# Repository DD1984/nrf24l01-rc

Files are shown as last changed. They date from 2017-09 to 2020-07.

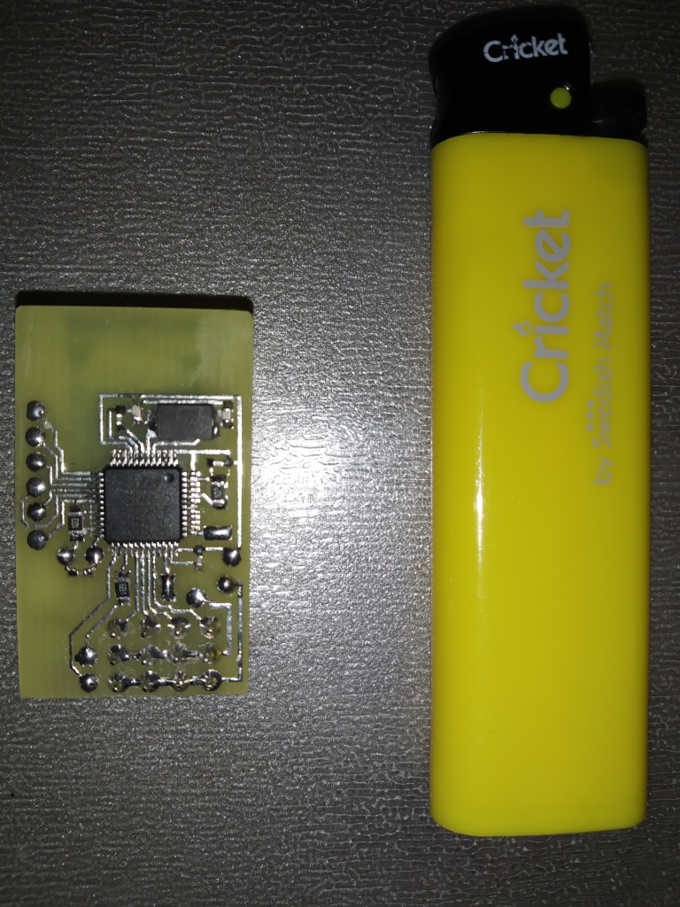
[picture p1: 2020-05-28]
stm32-nrf24l01-receiver/electronics/stm32f1/top.jpg

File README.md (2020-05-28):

# nRF24-based RC car receiver, compatible with HobbyKing HK310 and Turnigy 3XS

This project includes **electronics** and **firmware** to build **surface RC receivers** that can replace the HobbyKing [HKR3000](http://hobbyking.com/hobbyking/store/__12187__HK_3000_3ch_2_4ghz_FHSS_RX_suit_the_HK310_Transmitter.html) and [XR3100](http://hobbyking.com/hobbyking/store/__22910__HK3100_3ch_2_4ghz_FHSS_Micro_RX_suits_HK310_Turnigy_3XS_TX_.html) receivers. They can be used with the [HK300](http://hobbyking.com/hobbyking/store/__12177__HK_300_3_Channel_2_4ghz_FHSS_Ground_Radio.html), [HK310](http://hobbyking.com/hobbyking/store/__12181__HK_310_3_Channel_2_4ghz_FHSS_Ground_Radio.html) and [Turnigy 3XS](http://hobbyking.com/hobbyking/store/__24905__Turnigy_3XS_FHSS_2_4GHz_3_Channel_Radio_System.html) RC car radio systems.

The receivers make use of off-the-shelf inexpensive RF modules.

Two variants are provided:

- [lpc812-nrf24l01](lpc812-nrf24l01-receiver/): NRF24L01+ module plus a [NXP LPC812](http://www.nxp.com/products/microcontrollers/cortex_m0_m0/series/LPC800.html) MCU
- [nrf24le1](nrf24le1-receiver/): Using a NRF24LE1 module (integrated 8051 MCU)

**Now the third variant is available:**

- [stm32-nrf24l01](stm32-nrf24l01-receiver/): NRF24L01+ module plus a cheap STM32F030F4P6 MCU

**Fourth variant is available:**
- [stm32-nrf24l01](stm32-nrf24l01-receiver/): NRF24L01+ module (smd mount) plus a STM32F100C4T6 MCU (work on stm32vldiscovery too)

Technical information about the inner working of the receivers can be found
in **[hkr3000-info.md](doc/hkr3000-info.md)**.

## Advantages of the NRF24L01+ - LPC812 version

- Easily obtainable and very low cost NRF module (less than USD 1 including shipping in qty 10 on eBay, Aliexpress)
- Very precise servo pulses due to LPC812 timer hardware
- ARM Cortex-M0 32-bit CPU is easy to program for with the GCC ARM compiler
- No proprietary programmer required as the MCU has a ROM bootloader that can be flashed with an  USB-to-serial dongle
- Servo pulses can be updated down to every 5 ms (200 Hz). In theory this may provide better response but in practice the transmitter would need to be modified to fully take
advantage of this fact.
- UART output using the LANE Boys RC [preprocessor protocol](http://laneboysrc.blogspot.com/2012/12/pre-processor-for-diy-rc-light.html), e.g. to hook up the [DIY RC light controller](https://github.com/laneboysrc/rc-light-controller) with a single servo cable.

Downsides:

- Requires a PCB and intermediate SMD soldering skills
- No CPPM output (but it has a UART output that can carry CPPM-like data and more)

## Advantages of the NRF24LE1 version

- Low part count: NRF24LE1 module, voltage regulator, a few capacitors; done!
- Simple to build even on a breadboard
- CPPM output
- UART output using the LANE Boys RC [preprocessor protocol](http://laneboysrc.blogspot.com/2012/12/pre-processor-for-diy-rc-light.html), e.g. to hook up the [DIY RC light controller](https://github.com/laneboysrc/rc-light-controller) with a single servo cable. Baudrate is limited to 38400 though.

Downsides:

- NRF24LE1 module is more expensive than NRF24L01 and harder to find
- Requires special programming hardware. Multiple open-source versions can be found on the Internet.
- Servo pulses are software timed, hence slightly jittery despite using interrupts. Note that the firmware included in this project is improved over the original HKR3000 and XR3100 firmware, which regularly extends servo pulses by 16 us due to poor interrupt logic implementation.
- For the PCB provided in this project you need to get the NRF24LE1 module version that has an SMD crystal (size 21 x 15 mm)

The NRF24LE1 firmware included in this project can be compiled to be compatible with the HKR3000 and XR3100 hardware. However, since those receivers use the OTP version (NRF24LE1G) one would have to replace the chip with the NR24LE1E versions to be able to use it.

## Advantages of the NRF24L01+ - STM32F0 version

- Cheap and easily accessible MCU
- Free version of Keil MDK for STM32F0
- precise PWM due to hardware timer
- PWM frequency up to 200 Hz independ for CH1 and CH2/CH3
- One sided PCB with two jumper wire only

Downsides:

- 3 channel PWM output only

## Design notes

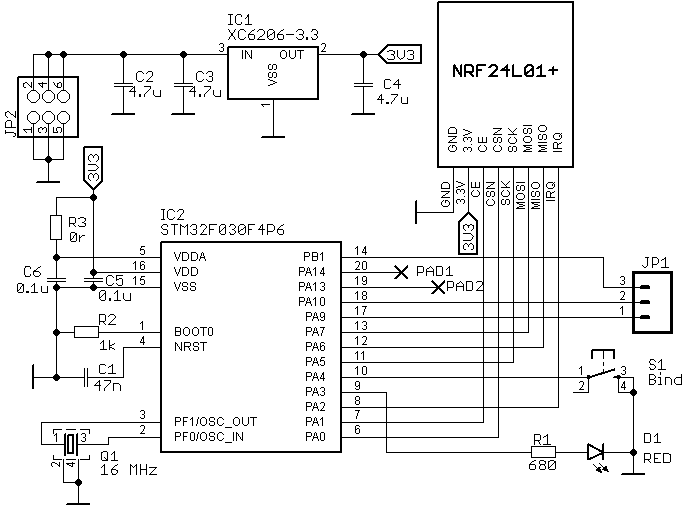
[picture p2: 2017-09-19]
stm32-nrf24l01-receiver/electronics/stm32f0/schematic.png

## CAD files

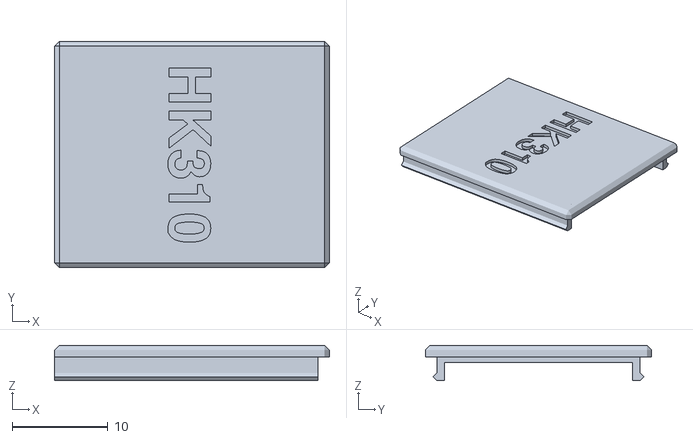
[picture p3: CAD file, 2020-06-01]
stm32-nrf24l01-receiver/electronics/stm32f1/box/box_top.stl
28.7 x 23.6 x 3.70

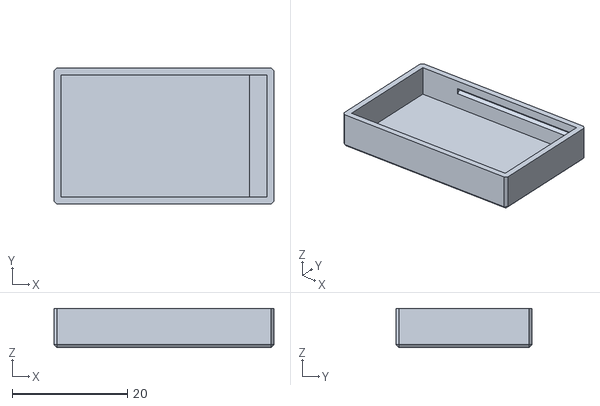
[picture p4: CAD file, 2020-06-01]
stm32-nrf24l01-receiver/electronics/stm32f1/box/box_bottom.stl
38.1 x 23.6 x 6.80

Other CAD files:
stm32-nrf24l01-receiver/electronics/stm32f1/box/rx_box.f3d

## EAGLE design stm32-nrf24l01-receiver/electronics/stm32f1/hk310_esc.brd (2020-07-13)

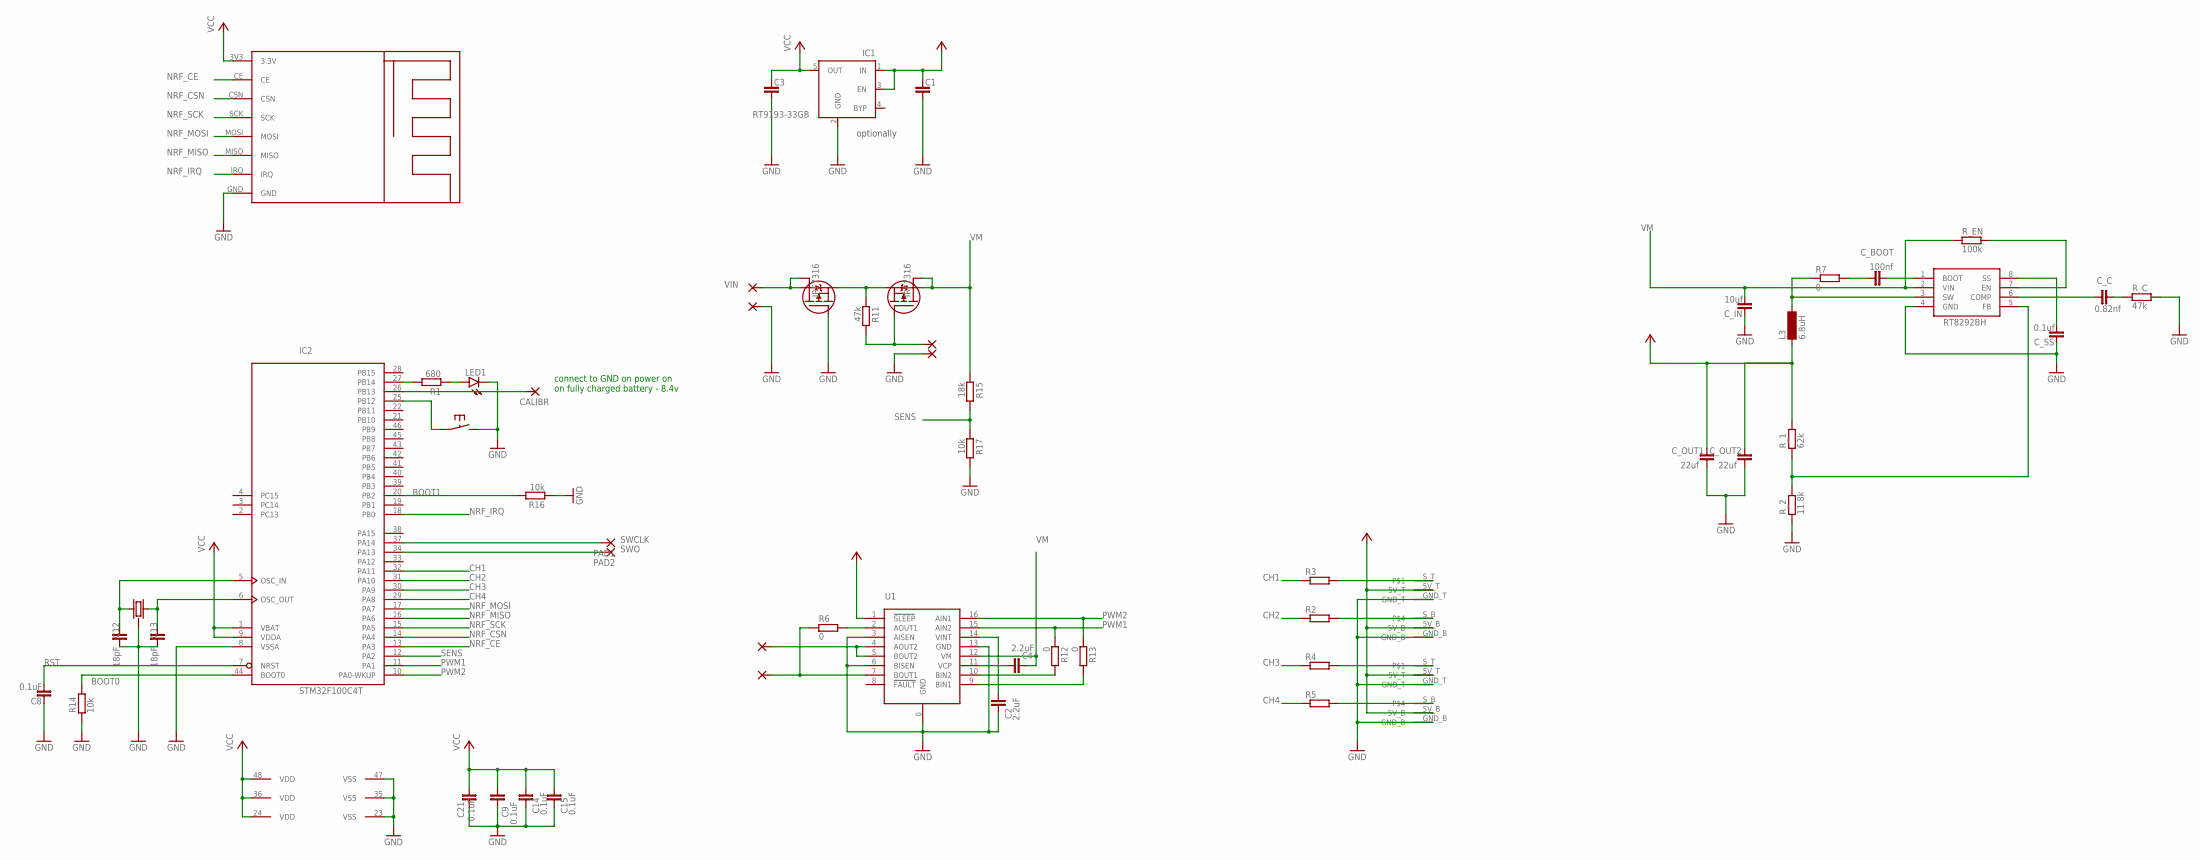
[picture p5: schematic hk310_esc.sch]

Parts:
C1, C3: C_0805; C0805
C2, C4: 2.2uF; C0805
C8, C9, C14, C15, C21: 0.1uF; C0603
C12, C13: 18pF; C0603
CALIBR: SMD2; SMD1,27-2,54
C_BOOT: 100nf; C0402
C_C: 0.82nf; C0402
C_IN: 10uf; C1206
C_OUT1, C_OUT2: 22uf; C0805
C_SS: 0.1uf; C0402
IC1: RT9193-33GB; SOT23-5
IC2: STM32F100C4T; LQFP48
L3: 6.8uH; MS85
LED1: LED; SMARTLED-TTW
PAD1, PAD2: SMD2; SMD1,27-2,54
PAD3, PAD4, PAD5, PAD6, PAD7, PAD8: WIREPADSMD5-1,8; 5-1,8
R1: 680; R0805
R2, R3, R4, R5: R-EU_R1206; R1206
R6, R7, R12, R13: 0; R1206
R11: 47k; R0805
R14, R16, R17: 10k; R0805
R15: 18k; R0805
RT8292BH: RT8292B; SO8-2
R_1: 62k; R0402
R_2: 11.8k; R0402
R_C: 47k; R0402
R_EN: 100k; R0402
U1: DRV8833; PWP16
U$1: NRF24MINI
U$2, U$3: PINHEAD_SMD
U$5: IRF7104; SO8-2
U$6: 8Mhz; CRYSTAL_3PINS
U$7: SMALL_BUTTON

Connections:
+5V: C1.1, C_OUT1.2, C_OUT2.2, IC1.1 (IN), IC1.3 (EN), L3.1, R_1.2, U1.1 (!SLEEP), U$2.5V_B, U$2.5V_T, U$3.5V_B, U$3.5V_T
BOOT0: IC2.44 (BOOT0), R14.2
BOOT1: IC2.20 (PB2), R16.2
CH1: IC2.32 (PA11), R3.1
CH2: IC2.31 (PA10), R2.1
CH3: IC2.30 (PA9), R4.1
CH4: IC2.29 (PA8), R5.1
GND: C1.2, C2.1, C3.2, C8.1, C9.1, C12.1, C13.1, C14.1, C15.1, C21.1, C_IN.1, C_OUT1.1, C_OUT2.1, C_SS.1, IC1.2 (GND), IC2.8 (VSSA), IC2.23 (VSS), IC2.35 (VSS), IC2.47 (VSS), LED1.C@1 (C), PAD5.1, PAD8.1, R14.1, R16.1, R17.2, RT8292BH.4 (GND), R_2.1, R_C.2, U1.0 (GND), U1.3 (AISEN), U1.6 (BISEN), U1.13 (GND), U$1.GND, U$2.GND_B, U$2.GND_T, U$3.GND_B, U$3.GND_T, U$5.4 (G), U$6.GND, U$7.2_1 (2), U$7.2_2 (2)
unnamed: IC2.25 (PB12), U$7.1_1 (1), U$7.1_2 (1)
unnamed: IC2.27 (PB14), R1.2
unnamed: LED1.A@1 (A), R1.1
unnamed: PAD3.1, U1.4 (AOUT2), U1.5 (BOUT2)
unnamed: R6.2, U1.2 (AOUT1)
unnamed: C2.2, U1.14 (VINT)
unnamed: C4.2, U1.11 (VCP)
unnamed: CALIBR.1, IC2.26 (PB13)
unnamed: C12.2, IC2.5 (OSC_IN), U$6.P$1
unnamed: R12.2, U1.10 (BIN2)
unnamed: R3.2, U$2.S_T
unnamed: R2.2, U$2.S_B
unnamed: R4.2, U$3.S_T
unnamed: R5.2, U$3.S_B
unnamed: PAD7.1, R6.1, U1.7 (BOUT1)
unnamed: C_BOOT.1, R7.2
unnamed: C13.2, IC2.6 (OSC_OUT), U$6.P$2
unnamed: PAD6.1, R11.2, U$5.2 (G)
unnamed: R13.2, U1.9 (BIN1)
unnamed: RT8292BH.7 (EN), R_EN.2
unnamed: C_SS.2, RT8292BH.8 (SS)
unnamed: C_BOOT.2, RT8292BH.1 (BOOT)
unnamed: L3.2, R7.1, RT8292BH.3 (SW)
unnamed: RT8292BH.5 (FB), R_1.1, R_2.2
unnamed: C_C.2, R_C.1
unnamed: C_C.1, RT8292BH.6 (COMP)
NRF_CE: IC2.13 (PA3), U$1.CE
NRF_CSN: IC2.14 (PA4), U$1.CSN
NRF_IRQ: IC2.18 (PB0), U$1.IRQ
NRF_MISO: IC2.16 (PA6), U$1.MISO
NRF_MOSI: IC2.17 (PA7), U$1.MOSI
NRF_SCK: IC2.15 (PA5), U$1.SCK
PWM1: IC2.11 (PA1), R12.1, U1.15 (AIN2)
PWM2: IC2.10 (PA0-WKUP), R13.1, U1.16 (AIN1)
RST: C8.2, IC2.7 (NRST)
SENS: IC2.12 (PA2), R15.2, R17.1
SWCLK: IC2.37 (PA14), PAD1.1
SWO: IC2.34 (PA13), PAD2.1
VCC: C3.1, C9.2, C14.2, C15.2, C21.2, IC1.5 (OUT), IC2.1 (VBAT), IC2.9 (VDDA), IC2.24 (VDD), IC2.36 (VDD), IC2.48 (VDD), U$1.3V3 (3.3V)
VIN: PAD4.1, U$5.5 (D), U$5.6 (D)
VIN_PROT: R11.1, U$5.1 (S), U$5.3 (S)
VM: C4.1, C_IN.2, R15.1, RT8292BH.2 (VIN), R_EN.1, U1.12 (VM), U$5.7 (D), U$5.8 (D)

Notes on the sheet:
optionally
connect to GND on power on on fully charged battery - 8.4v

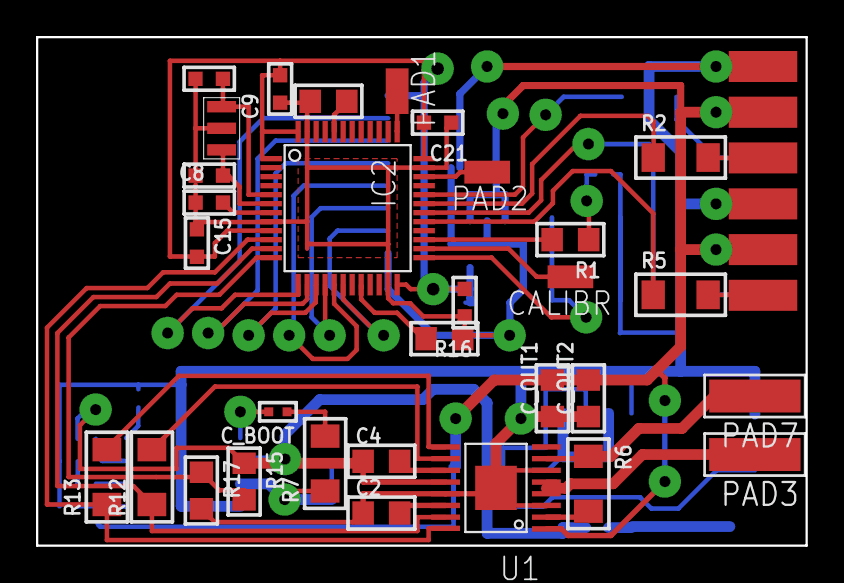
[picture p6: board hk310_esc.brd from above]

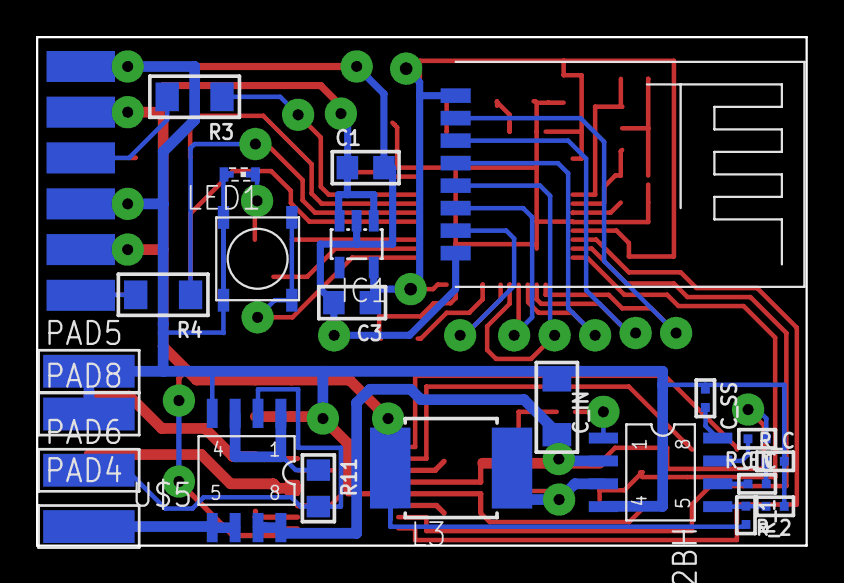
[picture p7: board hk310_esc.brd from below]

Board: 2 copper layers, 42.8 x 28.2 mm, 56 parts (25 on the bottom side), 50 nets.

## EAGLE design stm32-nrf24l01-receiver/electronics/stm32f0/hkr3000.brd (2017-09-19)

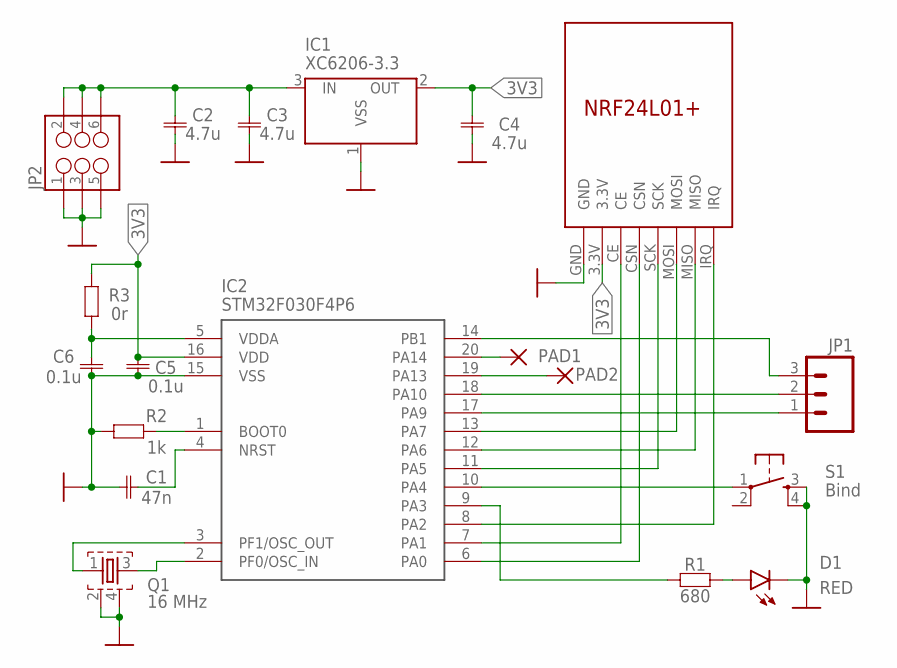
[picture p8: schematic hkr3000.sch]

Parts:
C1: 47n; 0402
C2, C3, C4: 4.7u; 0805
C5, C6: 0.1u; 0402
D1: RED; LED-0603
IC1: XC6206-3.3; XC6206_SOT-23
IC2: STM32F030F4P6; TSSOP-20
JP1: M03PTH; 1X03
JP2: M03X2POGO_PINS; 2X3_POGO
PAD1, PAD2: SMD2; SMD1,27-2,54
Q1: 16 MHz; FA-20H
R1: 680; 0402
R2: 1k; 0402
R3: 0r; 0603
S1: Bind; TACTILE-PTH
U$1: NRF24L01

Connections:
3V3: C4.P$2, C5.P$2, IC1.2 (OUT), IC2.16 (VDD), R3.P$2, U$1.3.3V
3V3-1: C6.P$2, IC2.5 (VDDA), R3.P$1
GND: C1.P$1, C2.P$1, C3.P$1, C4.P$1, C5.P$1, C6.P$1, D1.C, IC1.1 (VSS), IC2.15 (VSS), JP2.P$1 (1), JP2.P$3 (3), JP2.P$5 (5), Q1.2, Q1.4, R2.P$1, S1.3, S1.4, U$1.GND
unnamed: C2.P$2, C3.P$2, IC1.3 (IN), JP2.P$2 (2), JP2.P$4 (4), JP2.P$6 (6)
unnamed: D1.A, R1.P$2
unnamed: IC2.20 (PA14), PAD1.1
unnamed: IC2.11 (PA5), U$1.SCK
unnamed: IC2.12 (PA6), U$1.MISO
unnamed: IC2.13 (PA7), U$1.MOSI
unnamed: IC2.17 (PA9), JP1.1
unnamed: IC2.18 (PA10), JP1.2
unnamed: IC2.14 (PB1), JP1.3
unnamed: IC2.2 (PF0/OSC_IN), Q1.3
unnamed: IC2.3 (PF1/OSC_OUT), Q1.1
unnamed: C1.P$2, IC2.4 (NRST)
unnamed: IC2.1 (BOOT0), R2.P$2
unnamed: IC2.9 (PA3), R1.P$1
unnamed: IC2.19 (PA13), PAD2.1
unnamed: IC2.7 (PA1), U$1.CE
unnamed: IC2.6 (PA0), U$1.CSN
unnamed: IC2.8 (PA2), U$1.IRQ
unnamed: IC2.10 (PA4), S1.1

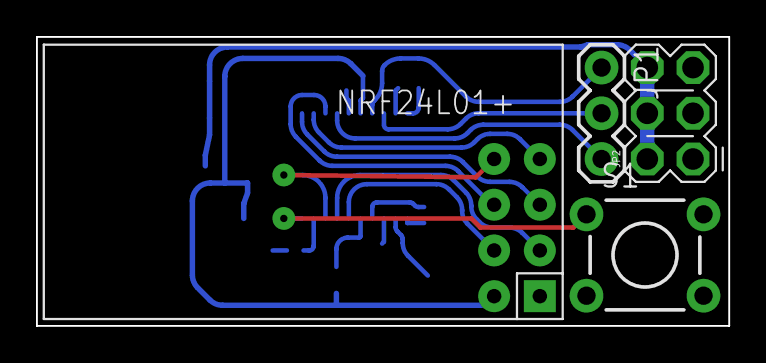
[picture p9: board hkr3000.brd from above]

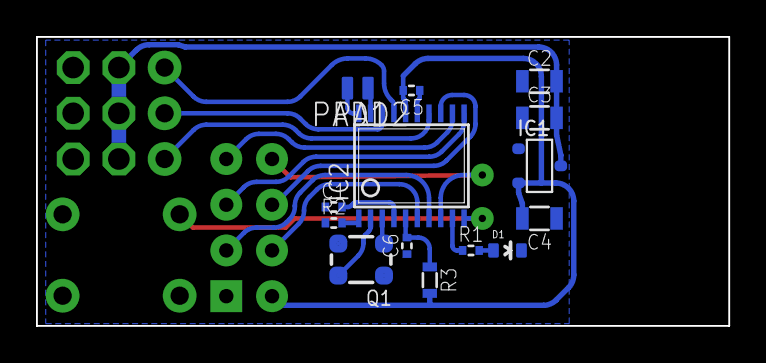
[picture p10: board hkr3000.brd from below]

Board: 2 copper layers, 38.5 x 16.1 mm, 19 parts (15 on the bottom side), 22 nets.

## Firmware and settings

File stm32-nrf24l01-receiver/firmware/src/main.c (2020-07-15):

/******************************************************************************

    Application entry point.

    Contains the main loop and the hardware initialization.

******************************************************************************/
#include <stdio.h>
#include <stdbool.h>

#include "platform.h"

#include "spi.h"
#include "rc_receiver.h"

#ifdef ESC
#include "esc.h"
#include "tune.h"
#include "adc.h"
#endif


#define IWDG_REFRESH        0x0000AAAA
#define IWDG_START          0x0000CCCC
#define IWDG_WRITE_ACCESS   0x00005555


// Global flag that is true for one mainloop every __SYSTICK_IN_MS
bool systick;
static volatile uint32_t systick_count;

// ****************************************************************************
static void service_systick(void)
{
    if (!systick_count) {
        systick = false;
        return;
    }

    systick = true;

    // Disable the SysTick interrupt. Use memory barriers to ensure that no
    // interrupt is pending in the pipeline.
    // More info:
    // http://infocenter.arm.com/help/index.jsp?topic=/com.arm.doc.dai0321a/BIHHFHJD.html
    SysTick->CTRL &= ~(1 << 1);
    __DSB();
    __ISB();
    --systick_count;
    SysTick->CTRL |= (1 << 1);      // Re-enable the system tick interrupt
}

// ****************************************************************************
#ifdef STM32F1
void EXTI0_IRQHandler (void)
#else
void EXTI2_3_IRQHandler (void)
#endif
{
    uint32_t status = EXTI->PR;
    uint32_t pending = 0;

#ifdef STM32F1
    if (status & EXTI_PR_PR0)
    {
        pending |= EXTI_PR_PR0;
        rf_interrupt_handler();
    }
#else
    if (status & EXTI_PR_PR2)
    {
        pending |= EXTI_PR_PR2;
        rf_interrupt_handler();
        //GPIO_LED_ON();
    }
#endif

    EXTI->PR = pending;
}

// ****************************************************************************
void TIM3_IRQHandler (void)
{
    uint16_t status = TIM3->SR;
    
    if (status & TIM_SR_UIF)
    {
        hop_timer_handler();
        status &= ~(TIM_SR_UIF);
    }

    TIM3->SR = status;
}

// ****************************************************************************
void SysTick_Handler (void)
{
    if (SysTick->CTRL & (1 << 16)) {       // Read and clear Countflag
        ++systick_count;
    }
}


// ****************************************************************************
static void init_hardware(void)
{
#ifdef STM32F1
    /**
     * PB14    - LED
     * PB13    - BAT CALIBR
     * PB12    - BIND
     *
     * PA4     - NRF_CSN
     * PA3     - NRF_CE
     * PB0     - NRF_IRQ
     * PA5     - NRF_SCK
     * PA6     - NRF_MISO
     * PA7     - NRF_MOSI
     *
     * PA11    - CH1 - TIM1_CH4
     * PA10    - CH2 - TIM1_CH3
     * PA9     - CH3 - TIM1_CH2
     * PA8     - CH4 - TIM1_CH1 - for future use
     */
    /* GPIO config */
    RCC->APB2ENR |= RCC_APB2ENR_IOPAEN | RCC_APB2ENR_IOPBEN | RCC_APB2ENR_IOPCEN | RCC_APB2ENR_AFIOEN;
    //PB14 - LED
    GPIOB->CRH &= ~(GPIO_CRH_CNF14 | GPIO_CRH_MODE14);
    GPIOB->CRH |= GPIO_CRH_MODE14_1; //2mhz out push-pull
    //PB12 - BIND
    GPIOB->CRH &= ~(GPIO_CRH_CNF12 | GPIO_CRH_MODE12);
    GPIOB->CRH |= GPIO_CRH_CNF12_1; //input push-pull
    GPIOB->BSRR = GPIO_BSRR_BS12; //pull up
#ifdef ESC
    //PB13 - BAT CALIBR
    GPIOB->CRH &= ~(GPIO_CRH_CNF13 | GPIO_CRH_MODE13);
    GPIOB->CRH |= GPIO_CRH_CNF13_1; //input push-pull
    GPIOB->BSRR = GPIO_BSRR_BS13; //pull up
#endif

    //PA4 - NRF_CSN, PA3 - NRF_CE
    GPIOA->CRL &= ~(GPIO_CRL_CNF4 | GPIO_CRL_MODE4 | GPIO_CRL_CNF3 | GPIO_CRL_MODE3);
    GPIOA->CRL |= GPIO_CRL_MODE4_0 | GPIO_CRL_MODE3_0; //10mhz out push-pull
    //PB0 - NRF_IRQ
    GPIOB->CRL &= ~(GPIO_CRL_CNF0 | GPIO_CRL_MODE0);
    GPIOB->CRL |= GPIO_CRL_CNF0_1; //input push-pull
    GPIOB->BSRR = GPIO_BSRR_BS0; //pull up

    //PA5, PA7
    GPIOA->CRL &= ~(GPIO_CRL_CNF5 | GPIO_CRL_MODE5 | GPIO_CRL_CNF7 | GPIO_CRL_MODE7);
    GPIOA->CRL |= GPIO_CRL_CNF5_1 | GPIO_CRL_MODE5_0 | GPIO_CRL_CNF7_1 | GPIO_CRL_MODE7_0; //10mhz alt push-pull
    //PA6 - floating input (do nothing)

    //PA11, PA10, PA9, PA8
    GPIOA->CRH &= ~(GPIO_CRH_CNF11 | GPIO_CRH_MODE11
                 | GPIO_CRH_CNF10 | GPIO_CRH_MODE10
                 | GPIO_CRH_CNF9 | GPIO_CRH_MODE9
                 | GPIO_CRH_CNF8 | GPIO_CRH_MODE8);
    GPIOA->CRH |= GPIO_CRH_CNF11_1 | GPIO_CRH_MODE11_0
               | GPIO_CRH_CNF10_1 | GPIO_CRH_MODE10_0
               | GPIO_CRH_CNF9_1 | GPIO_CRH_MODE9_0
               | GPIO_CRH_CNF8_1 | GPIO_CRH_MODE8_0; //10mhz alt push-pull


#else

    /**
     * PA0     - NRF_CSN
     * PA1     - NRF_CE
     * PA2     - NRF_IRQ
     * PA3     - LED
     * PA4     - BIND
     * PA5     - NRF_SCK
     * PA6     - NRF_MISO
     * PA7     - NRF_MOSI
     * PA9     - CH3 - TIM1_CH2
     * PA10    - CH2 - TIM1_CH3
     * PB1     - CH1 - TIM14_CH1
     */
    /* GPIO config */
    RCC->AHBENR |= RCC_AHBENR_GPIOAEN | RCC_AHBENR_GPIOBEN;

    GPIOA->MODER  &= ~(0x003CFFFF);
    GPIOA->MODER  |=   0x0028A845;
    GPIOA->OSPEEDR|=   0x003CCCCF;
    GPIOA->PUPDR  |=   0x00001110;
    GPIOA->AFR[0] &= ~(0xFFF00000);
    GPIOA->AFR[0] |=   0x00000000;
    GPIOA->AFR[1] &= ~(0x00000FF0);
    GPIOA->AFR[1] |=   0x00000220;
    

    GPIOB->MODER  &= ~(0x0000000C);
    GPIOB->MODER  |=   0x00000008;
    GPIOB->OSPEEDR|=   0x0000000C;
    GPIOB->AFR[0] &= ~(0x000000F0);
    GPIOB->AFR[0] |=   0x00000000;
    
#endif

    /* EXTI config */
#ifdef STM32F1
    AFIO->EXTICR[0] &= ~(AFIO_EXTICR1_EXTI0);
    AFIO->EXTICR[0] |=   AFIO_EXTICR1_EXTI0_PB;

    EXTI->FTSR |= EXTI_FTSR_TR0; /* Falling trigger event configuration */
    EXTI->IMR  |= EXTI_IMR_MR0;  /* Interrupt Mask on line 0 */
#else
    SYSCFG->EXTICR[0] &= ~(SYSCFG_EXTICR1_EXTI2);
    SYSCFG->EXTICR[0] |=   SYSCFG_EXTICR1_EXTI2_PA;
 
    EXTI->FTSR |= EXTI_FTSR_TR2; /* Falling trigger event configuration */
    EXTI->IMR  |= EXTI_IMR_MR2;  /* Interrupt Mask on line 2 */
#endif


    /* PWM Timers config */
#ifndef STM32F1
    RCC->APB1ENR |= RCC_APB1ENR_TIM14EN;
    TIM14->PSC = (24-1); /* Ftim = 2 Mhz */
    TIM14->ARR = ((2000000/CH1_FREQUENCY) - 1);
    TIM14->CCR1 = 2*1500; /* width = 1.5 ms */
    TIM14->CCMR1 |= TIM_CCMR1_OC1M_2 | TIM_CCMR1_OC1M_1 | TIM_CCMR1_OC1PE;
    TIM14->CCER |= TIM_CCER_CC1E;
    TIM14->CR1 |= TIM_CR1_CEN;
    TIM14->EGR = TIM_EGR_UG;	//	generate event and reload PSC
    while ((TIM14->SR & TIM_SR_UIF) == 0){}
    TIM14->SR = 0;
#endif
    
    RCC->APB2ENR |= RCC_APB2ENR_TIM1EN;   
#ifdef STM32F1
    TIM1->PSC = (SystemCoreClock / 1000000 / 2 - 1); /* Ftim = 2 Mhz */
    TIM1->ARR = ((2000000/CH2_CH3_FREQUENCY) - 1);
    TIM1->CCR1 = TIM1->CCR2 = TIM1->CCR3= TIM1->CCR4 = 2*1500; /* width = 1.5 ms */

    TIM1->CCMR1 = TIM_CCMR1_OC1M_2 | TIM_CCMR1_OC1M_1 | TIM_CCMR1_OC1PE
                | TIM_CCMR1_OC2M_2 | TIM_CCMR1_OC2M_1 | TIM_CCMR1_OC2PE;

    TIM1->CCMR2 = TIM_CCMR2_OC3M_2 | TIM_CCMR2_OC3M_1 | TIM_CCMR2_OC3PE
                | TIM_CCMR2_OC4M_2 | TIM_CCMR2_OC4M_1 | TIM_CCMR2_OC4PE;

    TIM1->CCER = TIM_CCER_CC1E  | TIM_CCER_CC3E | TIM_CCER_CC4E;
#ifndef DEBUG
    TIM1->CCER |= TIM_CCER_CC2E;
#endif

#else

    TIM1->PSC = (24-1); /* Ftim = 2 Mhz */
    TIM1->ARR = ((2000000/CH2_CH3_FREQUENCY) - 1);
    TIM1->CCR2 = 2*1500; /* width = 1.5 ms */
    TIM1->CCR3 = 2*1500; /* width = 1.5 ms */
    TIM1->CCMR1 = TIM_CCMR1_OC2M_2 | TIM_CCMR1_OC2M_1 | TIM_CCMR1_OC2PE;
    TIM1->CCMR2 = TIM_CCMR2_OC3M_2 | TIM_CCMR2_OC3M_1 | TIM_CCMR2_OC3PE;
    TIM1->CCER = TIM_CCER_CC2E | TIM_CCER_CC3E;
#endif

    TIM1->BDTR = TIM_BDTR_MOE;
    TIM1->CR1 |= TIM_CR1_CEN;
    TIM1->EGR = TIM_EGR_UG;	//	generate event and reload PSC
    while ((TIM1->SR & TIM_SR_UIF) == 0){}
    TIM1->SR = 0;
    
    /* hop Timer config */
    RCC->APB1ENR |= RCC_APB1ENR_TIM3EN;
#ifdef STM32F1
    TIM3->PSC = (SystemCoreClock / 1000000 - 1); /* Ftim = 1 Mhz */
#else
    TIM3->PSC = (48-1); /* Ftim = 1 Mhz */
#endif
    TIM3->ARR = (65536 - 1);
    TIM3->CNT = (65536 - 1);
    TIM3->CR1 =  TIM_CR1_DIR;
    TIM3->EGR = TIM_EGR_UG;	//	generate event and reload PSC
    while ((TIM3->SR & TIM_SR_UIF) == 0){}
    TIM3->SR = 0;
    TIM3->DIER = TIM_DIER_UIE;
    
    /* delay Timer config */
    RCC->APB2ENR |= RCC_APB2ENR_TIM16EN;
#ifdef STM32F1
    TIM16->PSC = (SystemCoreClock / 1000000 - 1); /* Ftim = 1 Mhz */
#else
    TIM16->PSC = (48-1); /* Ftim = 1 Mhz */
#endif
    TIM16->ARR = (65536 - 1);
    TIM16->CNT = 0;
    TIM16->CR1 = TIM_CR1_OPM;
    TIM16->EGR = TIM_EGR_UG;	//	generate event and reload PSC
    while ((TIM16->SR & TIM_SR_UIF) == 0){}
    TIM16->SR = 0;

#ifdef DEBUG
    uart_init();
#endif

#ifdef ESC
    pwm_timer_init();
    adc_init();
#endif


}

// ****************************************************************************
static void init_hardware_final(void)
{
    /* SysTick config */
#ifdef STM32F1
    SysTick_Config(SystemCoreClock / 1000 *__SYSTICK_IN_MS); // need /8 ???

    NVIC_SetPriority(EXTI0_IRQn, 0);
    NVIC_EnableIRQ(EXTI0_IRQn);

#else

    SysTick_Config(48000*__SYSTICK_IN_MS);
    NVIC_EnableIRQ(SysTick_IRQn);
    
    NVIC_SetPriority(EXTI2_3_IRQn, 0);
    NVIC_EnableIRQ(EXTI2_3_IRQn);
    
#endif

    NVIC_SetPriority(TIM3_IRQn, 1);
    NVIC_EnableIRQ(TIM3_IRQn);
    
}

// ****************************************************************************
void resetWatchdog (void);
void delay_us(uint32_t microseconds)
{
    TIM16->SR = 0;
    while (microseconds)
    {
        resetWatchdog();
        if (microseconds > 65535)
        {
            TIM16->CNT = 0;
            microseconds -= 65535;
        }
        else
        {
            TIM16->CNT = 65535 - microseconds;
            microseconds = 0;
        }
        TIM16->CR1 |= TIM_CR1_CEN;
        while ((TIM16->SR & TIM_SR_UIF) == 0);
        TIM16->SR = 0;	
    }
}


// ****************************************************************************
void startWatchdog (uint16_t ms)
{
    uint32_t reload = ((uint32_t)ms * LSI_VALUE)/(1000 * 32);
    IWDG->KR = IWDG_START;
    IWDG->KR = IWDG_WRITE_ACCESS;
    IWDG->PR = IWDG_PR_PR_0 | IWDG_PR_PR_1; /* divider = 32 */
    IWDG->RLR = IWDG_RLR_RL & reload;
    while (IWDG->SR) {};
    IWDG->KR = IWDG_REFRESH;
}

// ****************************************************************************
void resetWatchdog (void)
{
    IWDG->KR = IWDG_REFRESH;
}

// ****************************************************************************
int main(void)
{
    startWatchdog(200);
    init_hardware();
    init_spi();
    init_hardware_final();

    LOG("hello world\n");
    
#ifdef ESC
    start_sound();
    int bl = bat_level();
    if (bl)
        bat_beep(bl);
    else
        alarm_beep();
#endif
    
    // Wait a for a short time after power up before talking to the nRF24
    delay_us(20000);
    init_receiver();

    while (1)
    {
        resetWatchdog();
        service_systick();
        process_receiver();
    }
}

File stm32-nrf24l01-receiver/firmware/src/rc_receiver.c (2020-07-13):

#include <stdint.h>
#include <stdbool.h>

#include "platform.h"
#include "rc_receiver.h"
#include "persistent_storage.h"
#include "rf.h"

#ifdef ESC
#include "esc.h"
#endif


#define PAYLOAD_SIZE 10
#define ADDRESS_WIDTH 5
#define NUMBER_OF_HOP_CHANNELS 20
#define MAX_HOP_WITHOUT_PACKET 15
#define FIRST_HOP_TIME_IN_US 2500
#define HOP_TIME_IN_US 5000

#define FAILSAFE_TIMEOUT (640 / __SYSTICK_IN_MS)
#define BIND_TIMEOUT (5000 / __SYSTICK_IN_MS)
#define ISP_TIMEOUT (3000 / __SYSTICK_IN_MS)
#define BLINK_TIME_FAILSAFE (320 / __SYSTICK_IN_MS)
#define BLINK_TIME_BINDING (50 / __SYSTICK_IN_MS)

#define LED_STATE_IDLE 0
#define LED_STATE_RECEIVING 1
#define LED_STATE_FAILSAFE 2
#define LED_STATE_BINDING 3

#define BUTTON_PRESSED 0
#define BUTTON_RELEASED 1


extern bool systick;


uint16_t channels[NUMBER_OF_CHANNELS];
//uint16_t raw_data[2];
bool successful_stick_data = false;


static bool rf_int_fired = false;
static unsigned int led_state;
static unsigned int blink_timer;
static unsigned int bind_button_timer;

static uint8_t payload[PAYLOAD_SIZE];

static uint8_t failsafe_enabled;
static uint16_t failsafe[NUMBER_OF_CHANNELS];
static unsigned int failsafe_timer;

static uint8_t model_address[ADDRESS_WIDTH];
static bool perform_hop_requested = false;
static unsigned int hops_without_packet;
static unsigned int hop_index;
static uint8_t hop_data[NUMBER_OF_HOP_CHANNELS];

static bool binding_requested = false;
static bool binding = false;
static unsigned int bind_timer;
static const uint8_t BIND_CHANNEL = 0x51;
static const uint8_t BIND_ADDRESS[ADDRESS_WIDTH] = {0x12, 0x23, 0x23, 0x45, 0x78};
static uint8_t bind_storage_area[ADDRESS_WIDTH + NUMBER_OF_HOP_CHANNELS] __attribute__ ((aligned (4)));




// ****************************************************************************
static void initialize_failsafe(void) {
    int i;

    failsafe_enabled = false;
    failsafe_timer = FAILSAFE_TIMEOUT;
    for (i = 0; i < NUMBER_OF_CHANNELS; i++) {
        failsafe[i] = SERVO_PULSE_CENTER;
    }
}


// ****************************************************************************
static void output_pulses(void)
{
#ifdef STM32F1
    // RUDDER, THROTTLE, CH5
    TIM1->CCR4 = 2 * channels[0];
    TIM1->CCR3 = 2 * channels[1];
    TIM1->CCR2 = 2 * channels[2];

#ifdef ESC
    pwm_mode_t pwm_mode;
    uint16_t pwm_val;
    if (channels[1] < SERVO_PULSE_CENTER) {
        pwm_mode = BACKWARD;
        pwm_val = SERVO_PULSE_CENTER - channels[1];
    }
    else {
        pwm_mode = FORWARD;
        pwm_val = channels[1] - SERVO_PULSE_CENTER;
    }
    if (pwm_val > 500)
        pwm_val = 500;
    pwm_val = pwm_val * (1 << PWM_RES) / 500;
    pwm_run(pwm_mode, pwm_val);
#endif
    
#else
    TIM14->CCR1 = 2 * channels[0];
    TIM1->CCR3  = 2 * channels[1];
    TIM1->CCR2  = 2 * channels[2];
#endif
}


// ****************************************************************************
static uint16_t stickdata2ms(uint16_t stickdata)
{
    uint32_t ms;

    // ms = (0xffff - stickdata) * 3 / 4;
    ms = (0xffff - stickdata);
    ms = ((2100 - 900)*(ms)/(2750 - 1210) + 900) - (2100 - 900)*(1210)/(2750 - 1210);
    
    return ms & 0xffff;
}


// ****************************************************************************
// This code undos the value scaling that the transmitter nRF module does
// when receiving a 12 bit channel value via the UART, while forming the
// transmit packet.
//
// The transmitter calculates
//
//    value = (uart_data * 14 / 10) + 0xf200
//
// As such the input range via the UART can be 0x000 .. 0x9ff
// ****************************************************************************
/*
static uint16_t stickdata2txdata(uint16_t stickdata)
{
    uint32_t txdata;

    txdata = (stickdata - 0xf200) * 10 / 14;
    return txdata & 0xffff;
}
*/

// ****************************************************************************
static void stop_hop_timer(void)
{
    // Stop the Timer
    TIM3->CR1 &= ~(TIM_CR1_CEN);
    perform_hop_requested = false;
}


// ****************************************************************************
static void restart_hop_timer(void)
{
    
    TIM3->ARR = (HOP_TIME_IN_US - 1);
    TIM3->CNT = (FIRST_HOP_TIME_IN_US - 1);
    TIM3->CR1 |=  TIM_CR1_CEN;
    
    hops_without_packet = 0;
    perform_hop_requested = false;
}


// ****************************************************************************
static void restart_packet_receiving(void)
{
    stop_hop_timer();

    rf_clear_ce();
    hop_index = 0;
    hops_without_packet = 0;
    perform_hop_requested = false;
    rf_set_rx_address(DATA_PIPE_0, ADDRESS_WIDTH, model_address);
    rf_set_channel(hop_data[0]);
    rf_flush_rx_fifo();
    rf_clear_irq(RX_RD);
    rf_int_fired = false;
    rf_set_ce();
}


// ****************************************************************************
static void parse_bind_data(void)
{
    int i;

    for (i = 0; i < ADDRESS_WIDTH; i++) {
        model_address[i] = bind_storage_area[i];
    }

    for (i = 0; i < NUMBER_OF_HOP_CHANNELS; i++) {
        hop_data[i] = bind_storage_area[ADDRESS_WIDTH + i];
    }
}


// ****************************************************************************
static void binding_done(void)
{
    led_state = LED_STATE_IDLE;
    failsafe_timer = FAILSAFE_TIMEOUT;
    binding = false;
    binding_requested = false;

    restart_packet_receiving();
}
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

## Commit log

2017-09-17 add stm32 port
2017-09-19 add shematic and update README
    [hkr3000.brd, hkr3000.sch]
2020-05-23 [1/5] remove include stm32f0xx.h, because it included in platform.h
2020-05-23 [2/5] move startup files for stm32f0 in separated dir
2020-05-23 [3/5] add startup files for stm32f1 and Makefile
2020-05-23 [4/5] first work build for stm32vldiscovery, without channels output
2020-05-23 [5/5] add servo output CH2, CH3 on TIM1
2020-05-23 add stm32f1 linker script
2020-05-28 move stm32f0 PCB in separated dir
    [hkr3000.brd, hkr3000.sch]
2020-05-28 add stm32f1 PCB
    [DRILEGEND.CFG, hk310.brd, hk310.sch]
2020-05-28 - CH1 on TIM1 - change GPIOs for PCB - change ld script for stm32f100c4
2020-05-28 add firmware for stm32f1
2020-05-28 add stm32f1 version to readme
2020-05-28 readme: add info about stm32vldiscovery
2020-05-28 stm32f1 pcb photos
2020-06-01 stm32f1: add box 3d printing model
    [box_bottom.stl, box_top.stl, rx_box.f3d]
2020-07-13 add: - ESC support - battery health check (with calibration) - statup sound, batery level sound
    change:
    - persistent_storage - forsave many params
    - add uart debug
2020-07-13 pcb with esc
    [hk310_esc.brd, hk310_esc.sch]
2020-07-13 esc fw
2020-07-14 esc stop fix
2020-07-15 fix battery health check
    [adc.c, main.c]

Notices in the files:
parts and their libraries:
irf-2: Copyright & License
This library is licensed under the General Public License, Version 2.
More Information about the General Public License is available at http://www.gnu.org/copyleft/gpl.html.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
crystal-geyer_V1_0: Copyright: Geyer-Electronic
